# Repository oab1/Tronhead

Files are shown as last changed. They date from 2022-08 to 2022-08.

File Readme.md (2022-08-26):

# Tronhead
A CoreXY Toolhead for Voron printers

The goal of this project was to create a compact solution integrating what I've come to consider essential print head features (direct drive extruder, dockable magnetic z-probe, CAN board) without giving up the part cooling capabilities of dual 4010 radial fans. This toolhead achieves that while maintaing a very small form factor and low weight (~285 grams for the complete assembly less the mgn9h carts). Some key features:

- Integrated ANNEX Sherpa mini extruder (with significant modifications locating it closer to the hotend and x-axis and "fused" with hotend mount)
- Integrated Huvud PCB, w/forward folding hinge for easy access.
- Ducted hotend flow path with more open design for good airflow with 30mm axial fan.
- ANNEX Quickdraw dockable magnetic probe. 
- ANNEX K3 inspired Higher flow part cooling ducts

I've run it with single mgn9h rail (top), dual rail (front/bottom & top/bottom), and have settled on top/bottom dual mgn9h setup as that allowed tucking hotend as close to the x-rail as possible with the least amount of play in the mgn9h carts. I wanted to run with just a single mgn9h top rail configuration, but there was some play evident in that configuration.

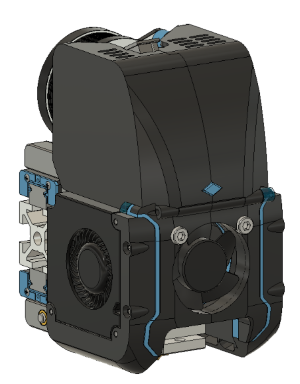
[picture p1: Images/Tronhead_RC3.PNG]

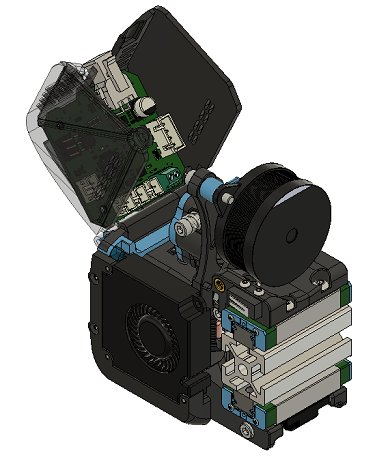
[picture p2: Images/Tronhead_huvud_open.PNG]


HOTEND Fan Duct Flow Path:

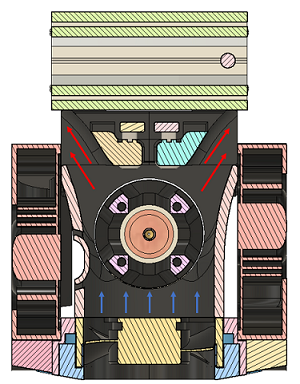
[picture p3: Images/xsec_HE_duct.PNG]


PART Fan Duct Flow Path:

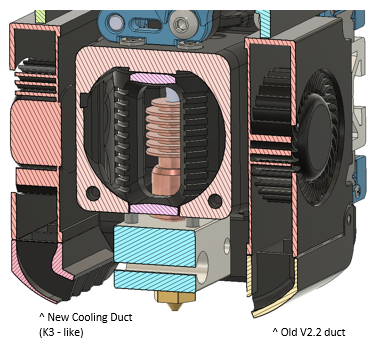
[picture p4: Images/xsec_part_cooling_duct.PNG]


Sherpa-Mini modifications:

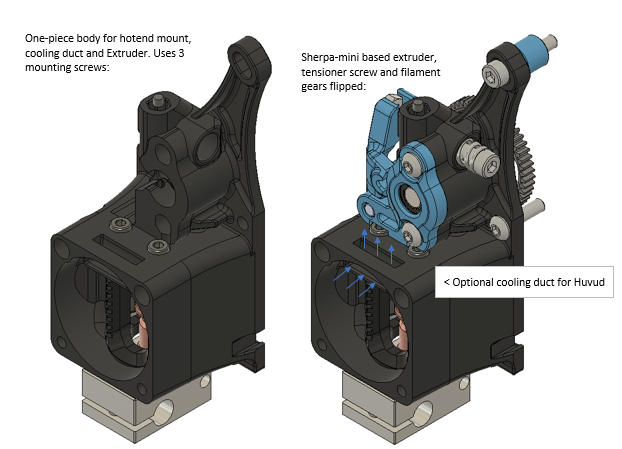
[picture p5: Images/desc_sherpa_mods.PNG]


- tensioner screw flipped and passes through body now to save space and prevents heat-set insert from pulling out.
- filament gears flipped. Pushes whole assembly with motor back another 8mm so overhang is less over x-rail.
- merged into hotend mount so the interface is rigid and supports sherpa at front end.

# Things that are specific to my setup!
- XY joints: Belt sits 2mm closer to extrusion, need to print and install XY joints (in STL's folder) to maintain proper alignment if installing on Voron.
- My NEMA14 motor has a 10-tooth drive gear on the output shaft (LDO). 8t and 9t are now also common, but may not have enough adjustment range to mesh properly, I haven't checked.

## Basic BOM:
- 30mm x 10mm axial fan (x1)
- 4010 radial fans (x2)
- Dragon Style hotend
- LDO NEMA 14 motor (currently configured for 10t drive gear)
- BMG 3mm hobbed gears and associated shafts and bearings
- ANNEX Quickdraw Probe
- Huvud toolhead PCB (optional)
- misc m3 screws (m3x30mm is the largest)
- m3 heatset inserts (5.0mm x 4.0mm)(x6)

I have a lot of time in this design so I would just appreciate that who shares or modifies my files credits them appropriately!
You can find me on Discord with any other questions, u/moab1#9591

## Credits

This design was possible because of the work and contributinons of many:
 
### Huvud Toolhead PCB
https://github.com/bondus/KlipperToolboard

### ANNEX Engineering Quickdraw Probe -
Toolhead uses this complete dockable probe solution from ANNEX:

https://github.com/Annex-Engineering/Quickdraw_Probe

### ANNEX Engineering Sherpa Mini Extruder
Extruder design based on this extruder from ANNEX:

https://github.com/Annex-Engineering/Sherpa_Mini-Extruder

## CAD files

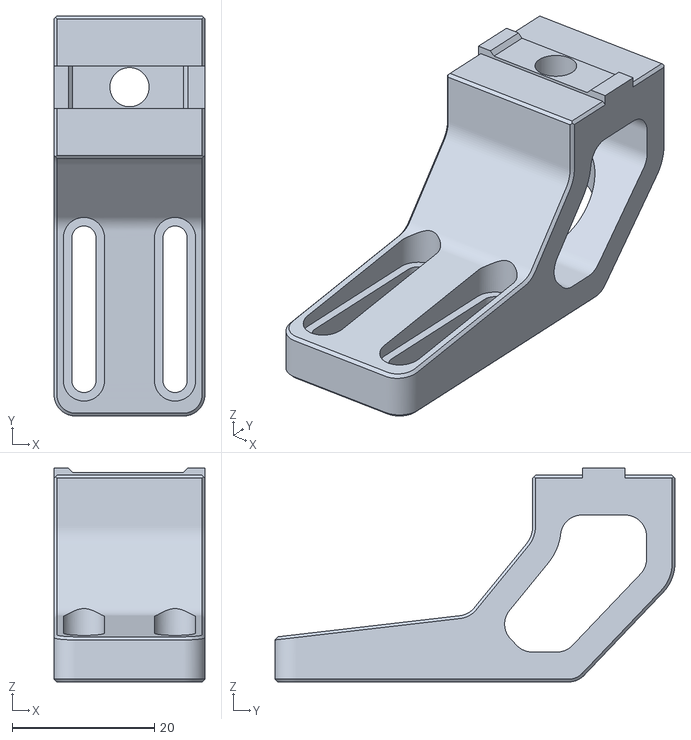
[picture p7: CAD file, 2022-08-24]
STL/QD_Gantry_Mount.stl
21.2 x 56.2 x 30.1

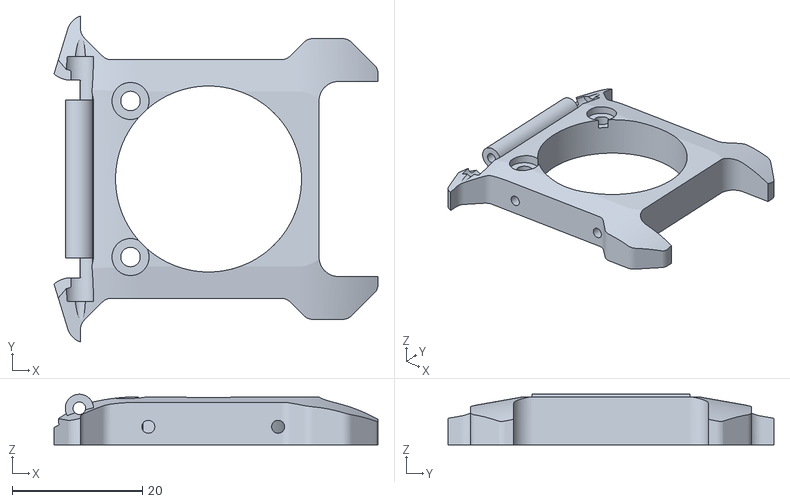
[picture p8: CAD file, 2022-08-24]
STL/Tronhead RC3/3010_fan_front_plate.stl
49.8 x 50.1 x 7.78

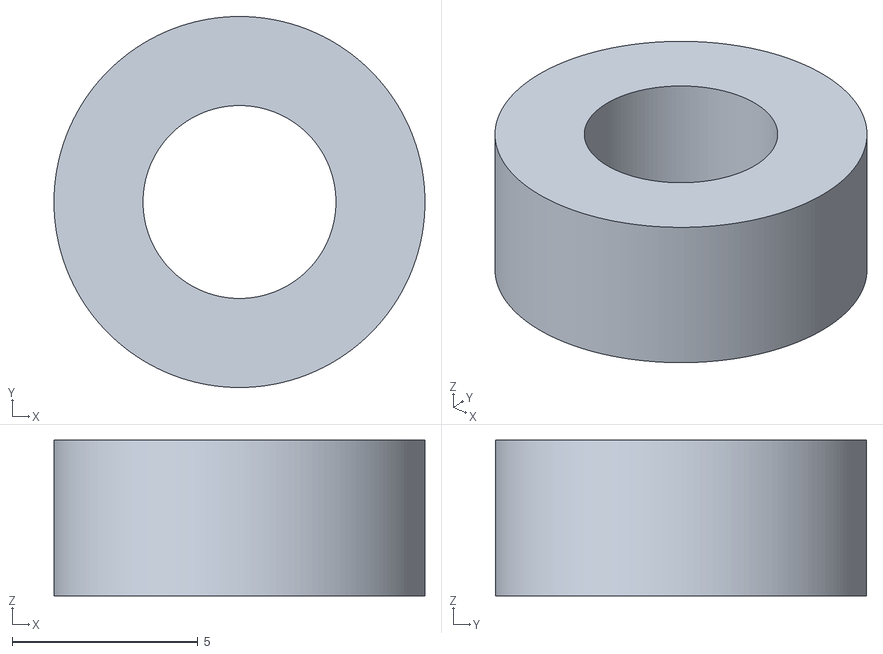
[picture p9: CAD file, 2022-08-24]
STL/XY Joints/Spacer A.stl
10.00 x 10.00 x 4.20

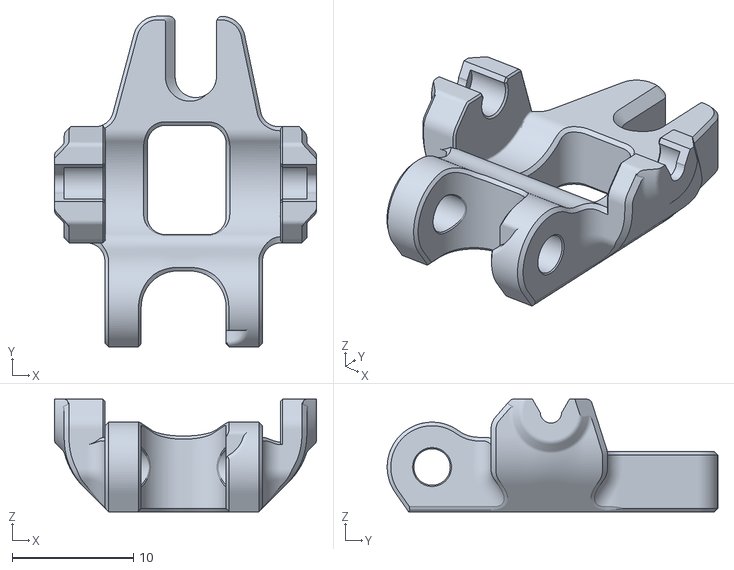
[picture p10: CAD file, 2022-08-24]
STL/Tronhead RC3/[a]_idler_arm^Tronhead_sherpa_mini.stl
21.6 x 27.3 x 9.30

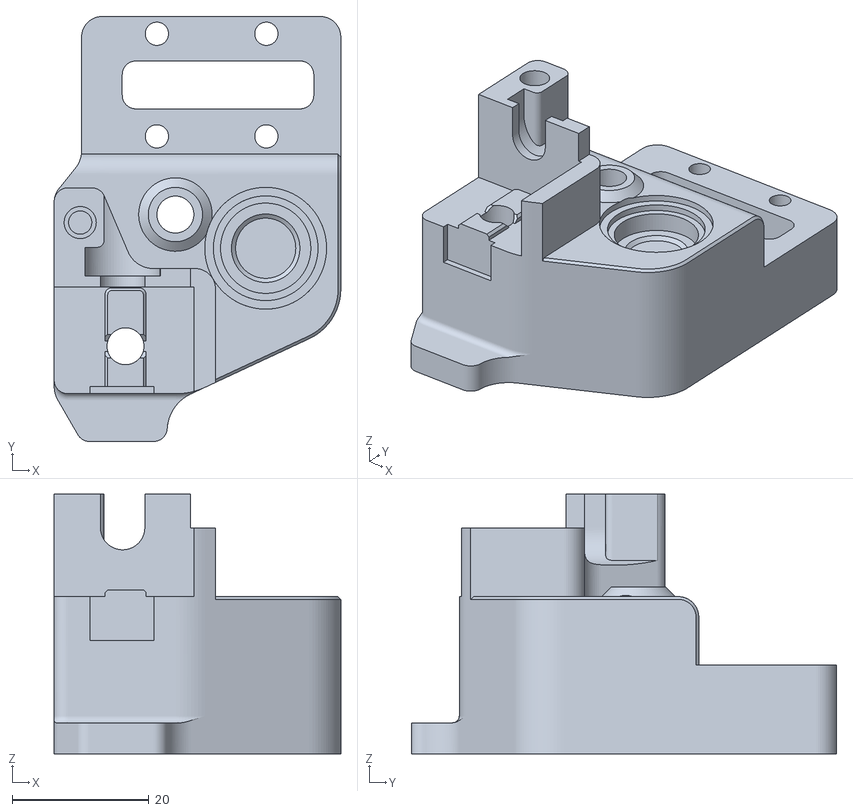
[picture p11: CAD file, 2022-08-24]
STL/XY Joints/XY Joint - Right - Bottom.stl
41.9 x 62.1 x 38.0

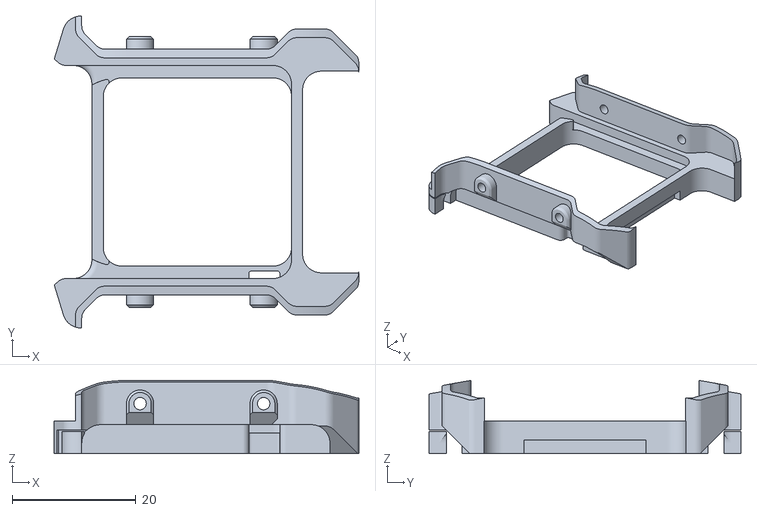
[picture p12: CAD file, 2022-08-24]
STL/Tronhead RC3/[a]_fan_back_plate.stl
49.2 x 50.4 x 11.8

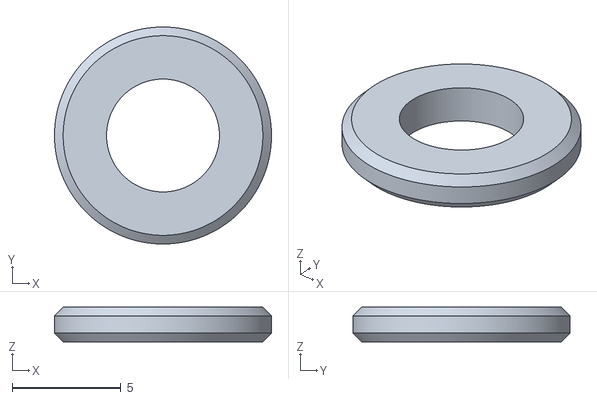
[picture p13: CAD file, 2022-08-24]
STL/XY Joints/Spacer B.stl
10.00 x 10.0 x 1.60

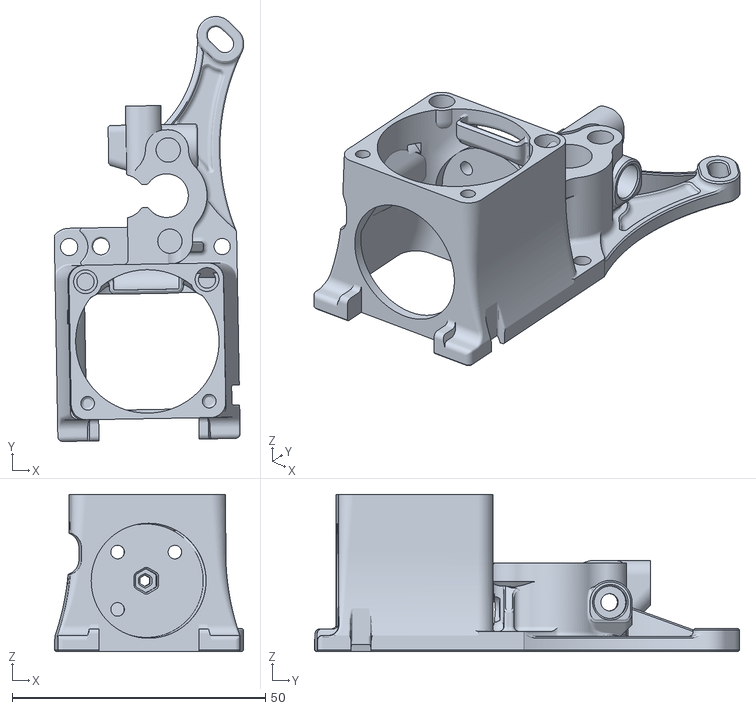
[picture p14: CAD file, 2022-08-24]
STL/Tronhead RC3/Tronhead_RC3_core (huvud cooling option).stl
37.4 x 83.9 x 31.1

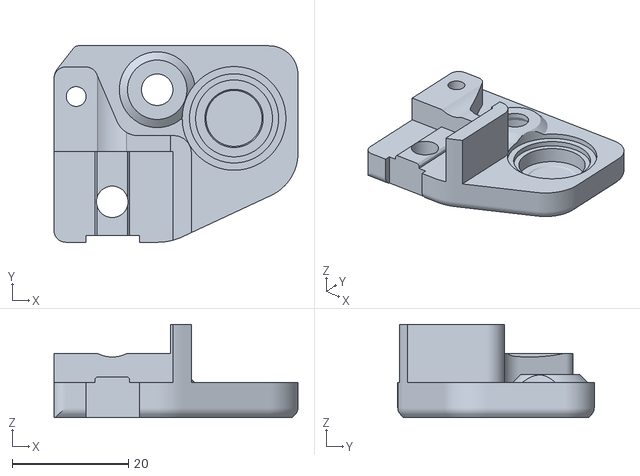
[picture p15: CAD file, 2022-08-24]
STL/XY Joints/XY Joint - Left - Top.stl
41.9 x 33.7 x 16.0

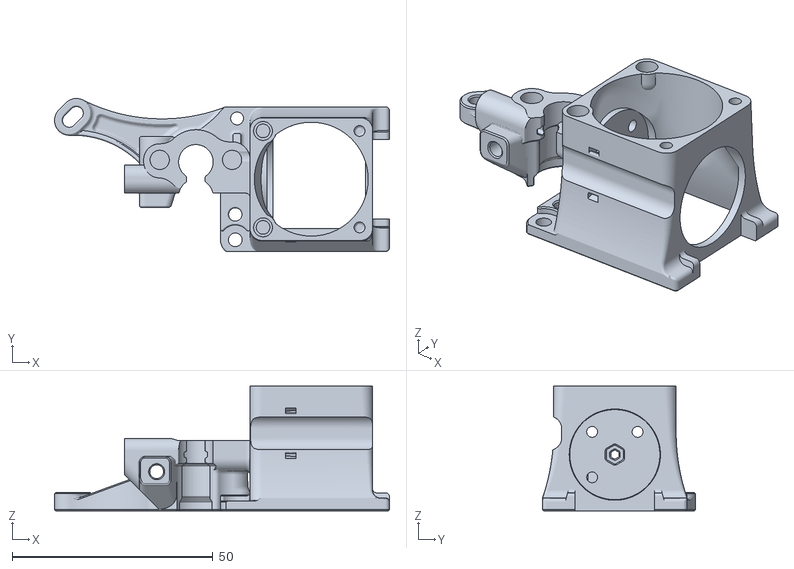
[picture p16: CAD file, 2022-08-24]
STL/Tronhead RC3/Tronhead_RC3_core.stl
83.3 x 38.1 x 31.1

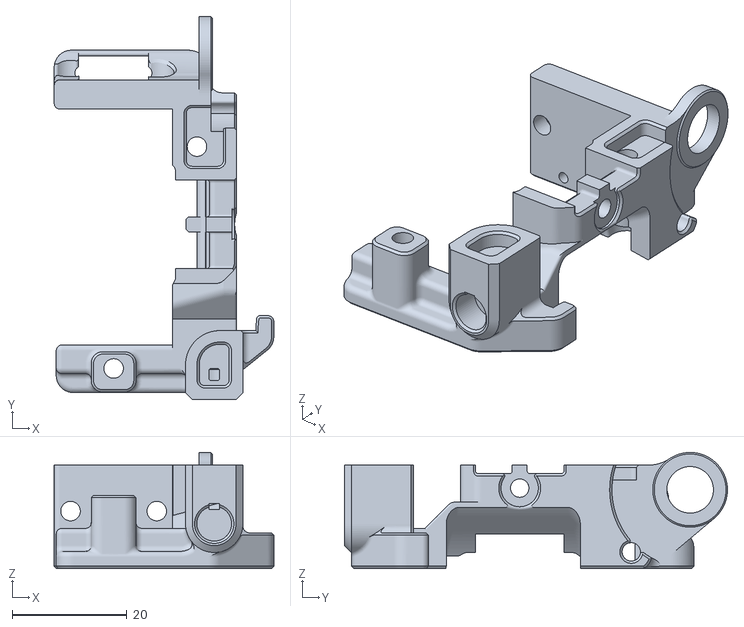
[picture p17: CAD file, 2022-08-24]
STL/Tronhead RC3/X-Carriage_RC3 (R).stl
38.2 x 66.7 x 20.2

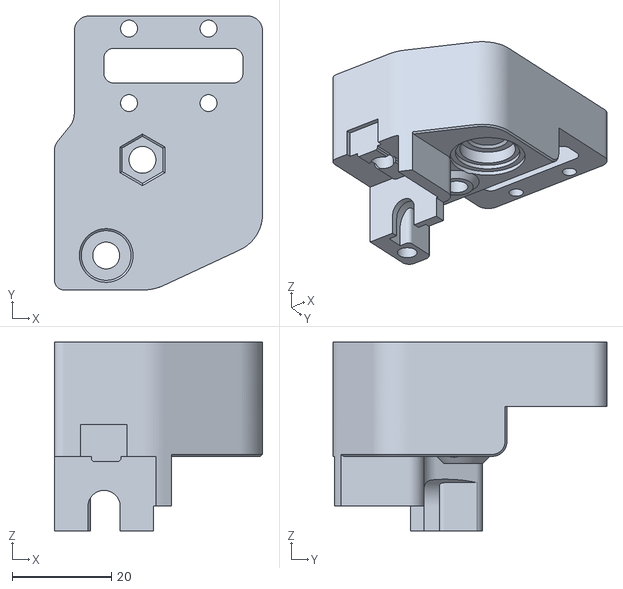
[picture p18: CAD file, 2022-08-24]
STL/XY Joints/XY Joint - Left - Bottom.stl
41.9 x 55.1 x 38.0

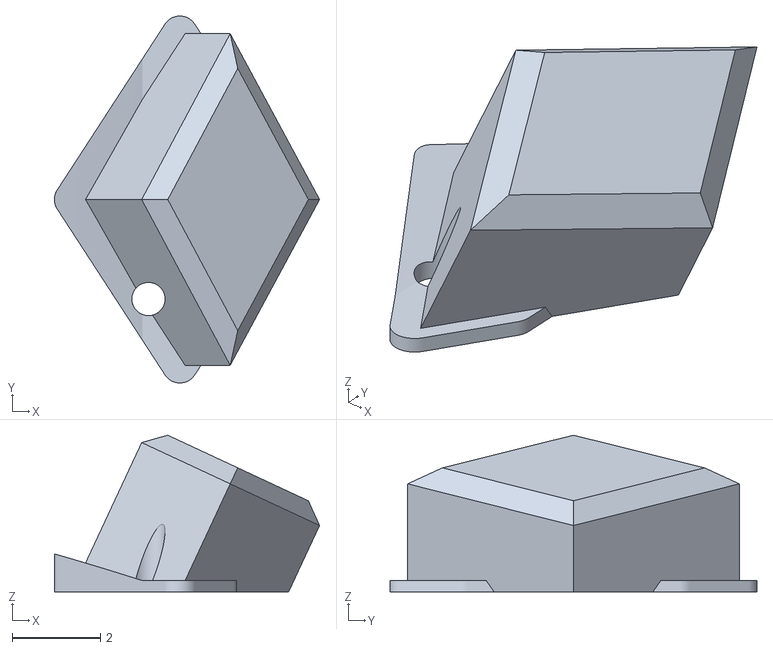
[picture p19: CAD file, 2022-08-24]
STL/Tronhead RC3/[a]_Diamond_logo.stl
6.00 x 8.30 x 3.54

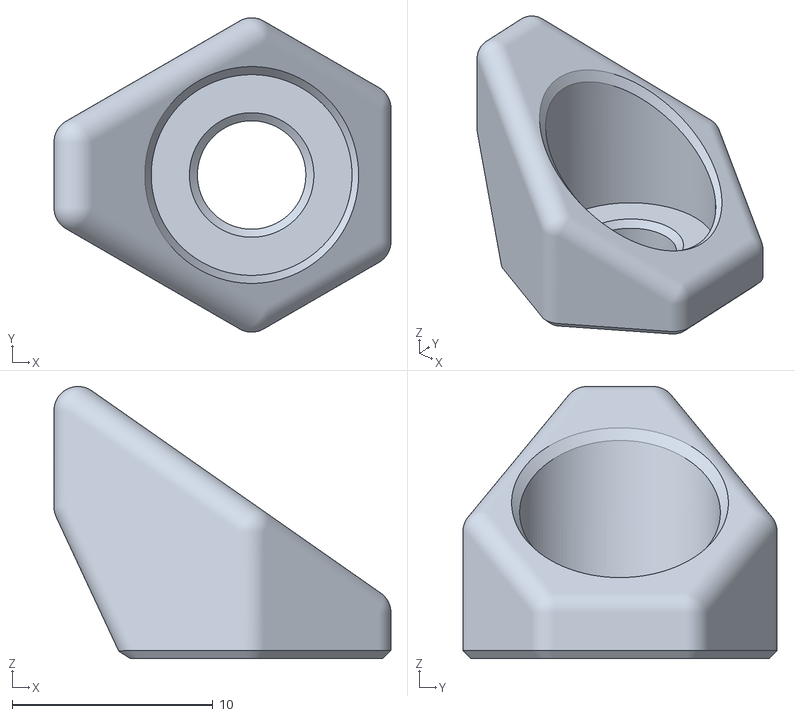
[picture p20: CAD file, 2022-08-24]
STL/XY Joints/End_Stop_Bumper.stl
16.8 x 15.7 x 13.6

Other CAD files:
STL/XY Joints/XY Joint - Right - Top.stl
STL/Tronhead RC3/Motor Spacer.stl
STL/Tronhead RC3/Connector_Cover (L).stl
STL/Tronhead RC3/housing_core^Tronhead_sherpa_mini (+cooling duct).stl
STL/Tronhead RC3/4010 Part Fan Duct (L).stl
STL/Tronhead RC3/4010 Part Fan Duct (R).stl
STL/Tronhead RC3/Connector_Cover (R).stl
STL/Tronhead RC3/X-Carriage_RC3 (L).stl
STL/Tronhead RC3/X-Carriage_RHS_RC3.stl
STL/Tronhead RC3/[a]_sherpa_front_housing.stl

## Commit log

2022-08-24 Organized STL files
    [3010_fan_front_plate.stl, 4010 Part Fan Duct (L).stl, 4010 Part Fan Duct (R).stl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]
2022-08-24 Fix print orientation of STL's
    [3010_fan_front_plate.stl, Connector_Cover (L).stl, Motor Spacer.stl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]
2022-08-24 remove obsolete files
    [1011_china_chain_mount.stl, Connector_Cover_Left.stl, Connector_Cover_Right.stl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]
